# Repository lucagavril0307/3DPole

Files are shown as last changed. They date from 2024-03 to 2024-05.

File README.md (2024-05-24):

# 3DPole

10.04.2024 -> S-a adăugat un model CAD complet (dimensiunile pot diferi în viața reală, componentele pot diferi în viața reală, nu s-au făcut cablaje și/sau animații în modelul CAD)

11.04.2024 -> S-a adaugat un folder cu manuale ale componentelor, scheme electrice și/sau alte informații legale.

21.05.2024 -> S-a adăugat diagrama de cablare completă ( nu știu cum am ratat asta:3 );

23.05.2024 -> Configurația finală* a software-ului a fost publicată
- Este încă o versiune beta, testarea trebuie făcută pentru Marlin 2.1.x în sine și pentru configurația mea.

  24.05.2024 -> S-a adăugat noua documentaie în română precum și s-au făcut update-uri la documente deja existente.

3D Pole este o imprimanta 3 bazată pe Coordonate Polare construită din materiale “off-the-shelf” și/sau printate 3D.

## Proiectat de Luca Szilagyi de la Colegiul Național “Vasile Lucaciu” Baia Mare sub coordonarea dnei. profesoare Filip Adela

Toate fișierele pentru fișierele imprimabile 3D sunt furnizate în folderul 3D CAD, soft-ul este furnizat în folderul Software (configurația se afla sub irectorul Marlin, mai precis Configuration.h si Configuration_adv.h)

Acest proiect a necesitat piese imprimate 3D personalizate, precum și cabluri sertizate personalizate și firmware configurabil bazat pe Marlin.

!! Imprimanta dispune de protecție termică, dar este încă un prototip, așa că fiți conștienți de riscuri!

!! Sistemul folosește o sursă de alimentare de 24V 12,4 A. În timp ce metaluli firelor nu este expus, este totuși periculos!

# Imprimante Polare

Majoritatea oamenilor au auzit de imprimantele 3D Cartesiane, iar alții știu și despre imprimantele CoreXY.
Adevărul este că toată industria imprimării 3D s-a schimbat foarte mult în ultimii 20 de ani. Avem tipuri aparent nesfârșite de imprimante 3D.

Există imprimante carteziene normale care au crescut odată cu producția chineză de imprimante 3D după expirarea brevetului, există și imprimante CoreXY care au devenit mai populare la mijlocul anului 2020 și imprimantele Delta care au înregistrat o creștere în 2011 și încă una în 2024 odată cu lansarea. de imprimante rapide de la Flsun.

Fiecare tip de imprimantă are propriile defecte și puncte de vânzare, tipul cartezian de imprimantă este ieftină și ușor de întreținut, este, de asemenea, ușor de construit dacă doriți, dar nu este rapidă și multe probleme de calitate a vieții apar cu timpul. CoreXY sunt (cel mai adesea) mari, rapide și în general, dezavantajul lor este prețul și sistemul complex de mișcare. Imprimantele Delta sunt înalte și subțiri, la prima vedere înfricoșătoare, dar de fapt sunt mai rapide decât imprimantele carteziene (și modelele mai noi sunt chiar mai rapide decât cele CoreXY), ușor de întreținut, dar spațiul de imprimare este limitat și tind să fie destul de înalte și greu de incadrat intr-un spatiu normal.

Pe lângă aceste 3 tipuri majore de imprimante (când vorbim de mașini de tip FDM) există mașini cu 5 axe, CoreXZ, mașini de calitate industrială și preferatul meu , Imprimante Polaree.

Imprimantele Polare împrumută ceva de la toate cele 3 mari tipuri de imprimante FDM. Sunt ieftine și ușor de asamblat precum imprimantele carteziene, rapide* și fiabile ca frații lor CoreXY, ușor de extins și cu aspect înfricoșător (când vine vorba de matematică), la fel ca imprimantele Delta.

*Deși pot fi rapide, acest prototip nu este nimic din toate acestea, am ales lentă și robustă, deoarece oferă cele mai bune rezultate, cu multe reglaje, puteți transforma acest proiect într-o mașină rapidă.

Imprimantele carteziene tradiționale folosesc (după cum sugerează și numele) un sistem cartezian standard cu 3 axe, aveți valoarea X care vă spune cât de stânga sau dreapta este un punct ,valoarea Y care determină mișcarea înainte și înapoi și variabila Z care dictează înălţimea. CoreXY este oarecum același, dar X și Y sunt un sistem 2 în 1 realizat folosind o rutare ingenioasă a curelelor care mișcă capul de imprimare cu precizie cu axa Z deplasând întregul pat în sus și-n jos. Imprimantele Delta au un pat fix  nu par să aibă 3 axe diferite, au 3 axe paralele conectate la capul de imprimare cu 3 brațe, prin deplasarea celor 3 axe în diferite moduri puteți ajunge în orice punct din spațiul de imprimare, deși spațiul de imprimare nu este un cilindru, ci mai mult un con la vârf datorită acestui sistem de mișcare.

Imprimantele Polare arată ca imprimantele carteziene (numai ca aspect) cu 3 axe separate, dar un ochi atent va vedea că axa X este mai scurtă decât de obicei. Datorită unui sistem de mișcare Polară, axa X trebuie să aibă doar jumătate din dimensiunea patului, reducând astfel costurile materialelor, greutatea pe axa de imprimare și făcând o călătorie completă mai rapidă.

imagine

Pentru a obține poziția unui punct în planul XY veți avea nevoie de un unghi și de o distanță (r și Θ), distanța ia valori de la 0 (punctul din mijloc al cercului) și raza cercului (jumătate din dimensiunea patului, deci va fi axa X) în timp ce Θ este un unghi (deci de la 0 la 360 <sau 2π în radiani>, adică rotația patului, deci axa Y). Axa Z dictează doar cât de înalt este punctul menționat.

 # Specificații și informații despre imprimantă

 După cum am explicat mai devreme, este o imprimantă Polară, cu unele caracteristici realizate folosind imprimarea 3D.
 Cum ar putea funcționa asta?
 În primele timpuri ale imprimării 3D a existat o comunitate numită RepRap care dorea să facă imprimarea 3D mai accesibilă, deoarece la acea vreme, era destinată doar industriei sau bogaților. Au proiectat imprimante care ar putea fi ieftine și suficient de bune pentru ca oricine să le facă,. La acel moment nu puteai cumpăra o imprimantă prefabricată, trebuia să o construiești singur. În această perioadă s-au făcut o mulțime de noi descoperiri care au adus imprimarea 3D la ceea ce este astăzi.
 
Comunitatea RepRap a fost o mulțime de entuziaști care au făcut ca proiectele de imprimante i să fie ușor de recreat. Deoarece nu aveau acces la echipamente industriale, majoritatea pieselor dintr-o imprimantă 3d trebuiau imprimate 3d. Ei au decis ca generația 1 de imprimante să fie făcute cu piese  imprimate 3d de la mașini industriale și următoarea generație de imprimante ar putea avea toate piesele de care au nevoie de la mașina de prima generație, așa că, cu o singură mașină puteți face alta care poate face altul și așa mai departe. Tendința a prins din urmă și chiar a ajuns în zilele noastre.
Echipa de design Voron, cunoscută pentru imprimantele lor rapide, are propriul program „Print it forward” în care (pentru o sumă de bani) cineva care are deja o imprimantă Voron va imprima piesele de care aveți nevoie (și piesele estetice dacă doriți) și mai târziu, puteți imprima aceleași piese pe aparatul dvs. pentru altcineva.

Captură de ecran 2024-05-21 192004

Am decis să fac acest proiect în același spirit cu toate piesele printate 3D pentru această imprimantă putând fi realizate pe noua imprimantă.
Unele decizii trebuiau luate în ceea ce privește designul, nu mi-au plăcut niciodată imprimantele voluminoase (sau cele închise - chiar dacă au multe plusuri - deși am una). Axa X este inspirată de axa Ender 3 din două mari motive, pentru a fi clar că împrumută ceva de la imprimantele carteziene și pentru că, dacă nu este stricat, de ce sa il repar?

Designul este testat în timp și cred că arată bine în contrast cu întreaga imprimantă.
În ceea ce privește celelalte părți, sunt modele noi făcute de mine, pe lângă hotend-ul care este un model HERO ME și montura pentru axa X-E0 Care este un Model Ender 3.

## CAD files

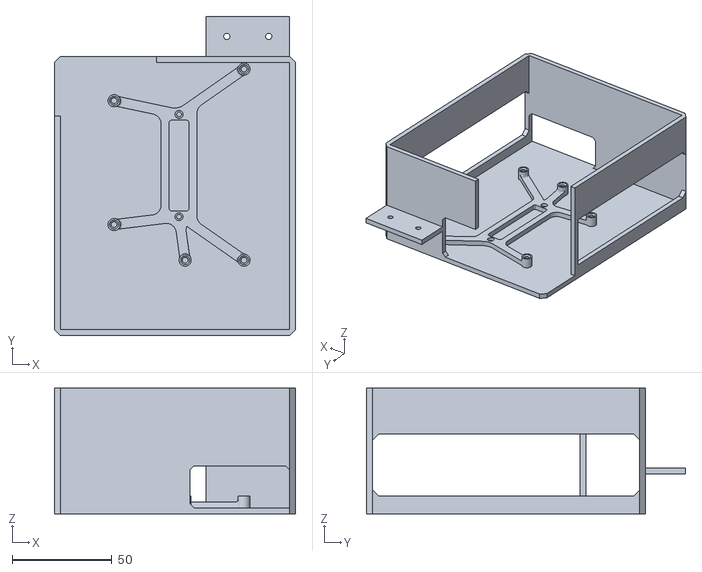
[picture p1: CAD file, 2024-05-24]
3DCADFiles/BTTCase.stl
121.0 x 160.0 x 63.0

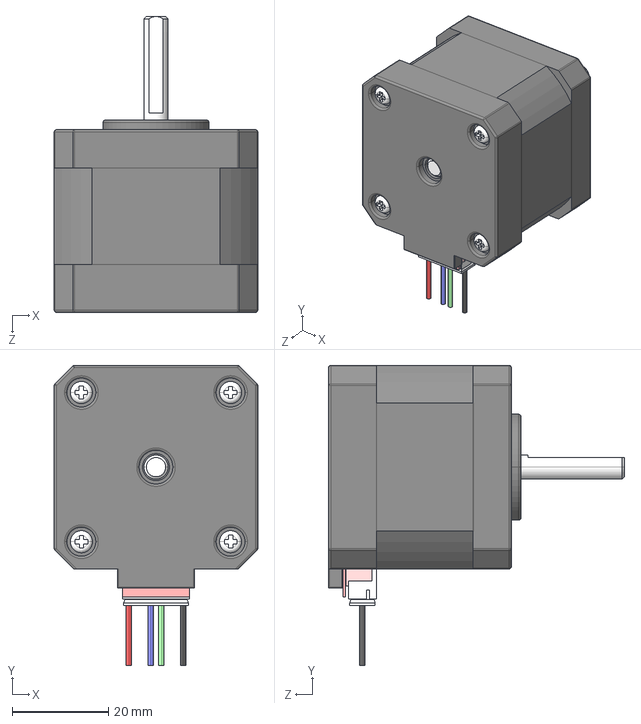
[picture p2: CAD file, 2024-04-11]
Wiring .Hardware Manuals and Documantation/17HE15-1504S.STEP
42.3 x 62.4 x 61.5 mm

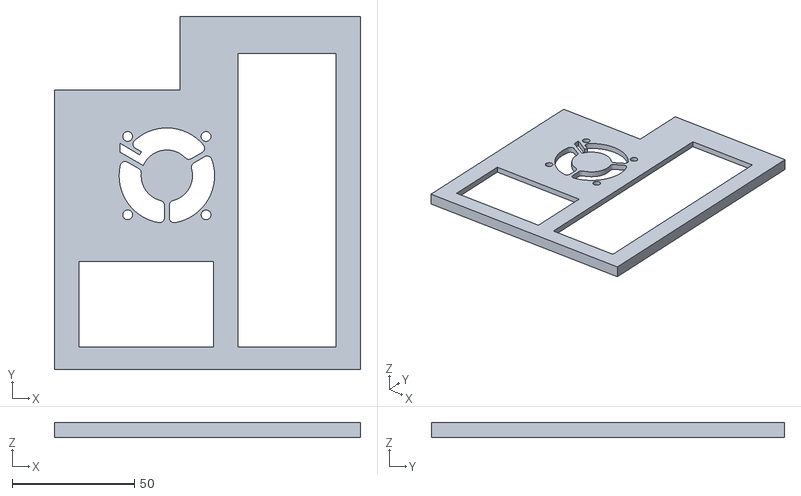
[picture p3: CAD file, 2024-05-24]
3DCADFiles/BTTTop.stl
125.2 x 144.2 x 6.00

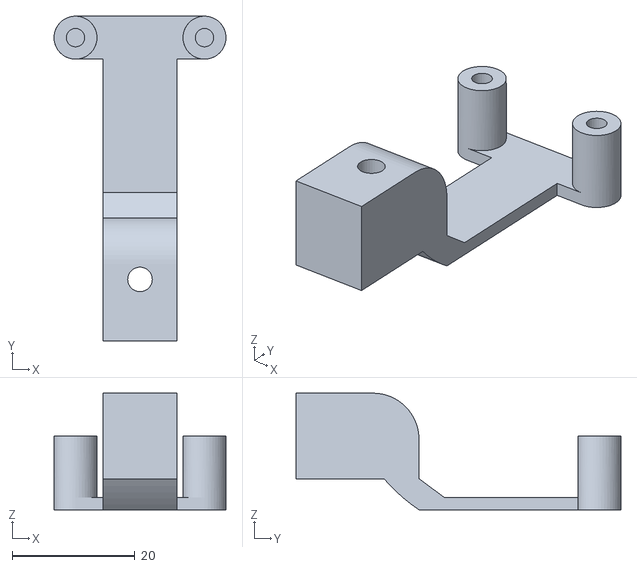
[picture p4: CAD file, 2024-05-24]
3DCADFiles/ZSwitch.stl
28.0 x 52.9 x 19.0

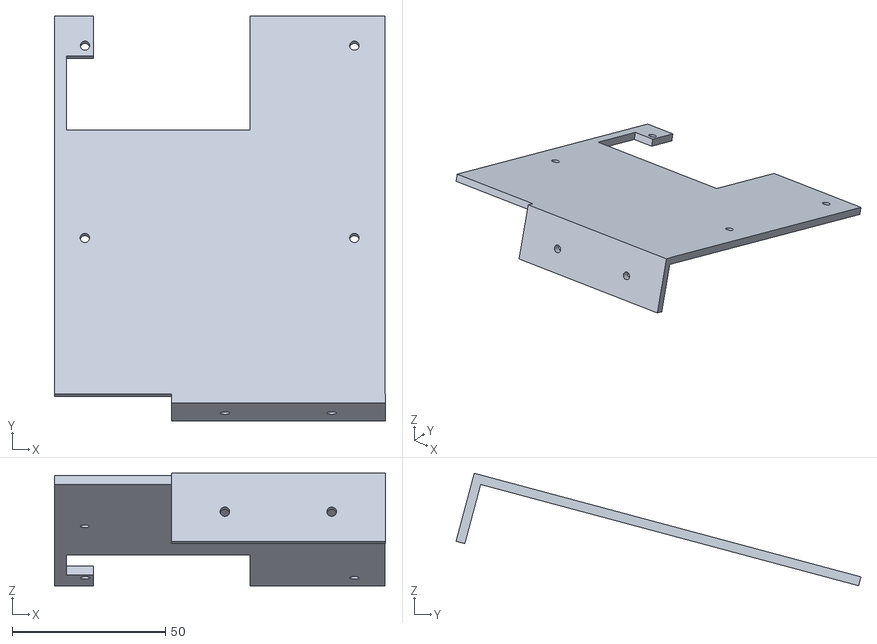
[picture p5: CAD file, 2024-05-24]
3DCADFiles/TFT35Case.stl
108.2 x 132.3 x 36.8

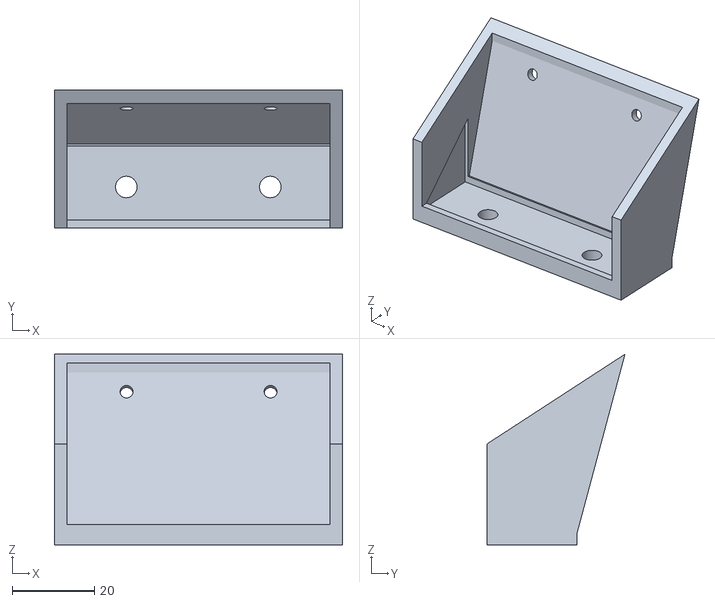
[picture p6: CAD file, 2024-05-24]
3DCADFiles/ScreenRiser.stl
70.2 x 33.6 x 46.5

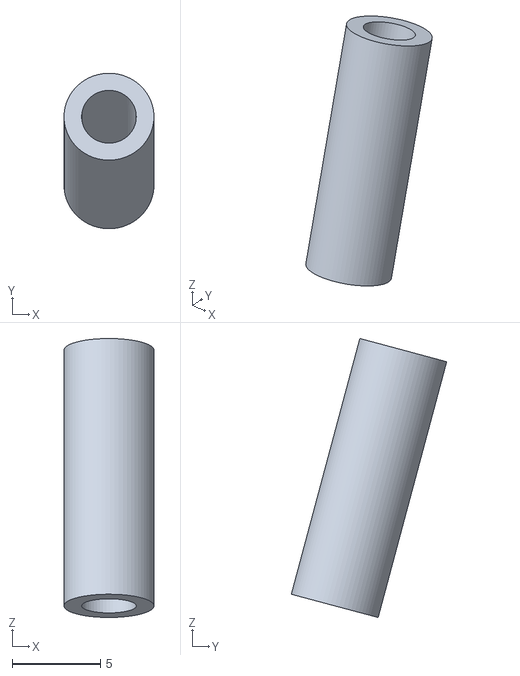
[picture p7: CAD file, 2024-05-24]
3DCADFiles/Standoff.stl
5.09 x 8.81 x 15.8

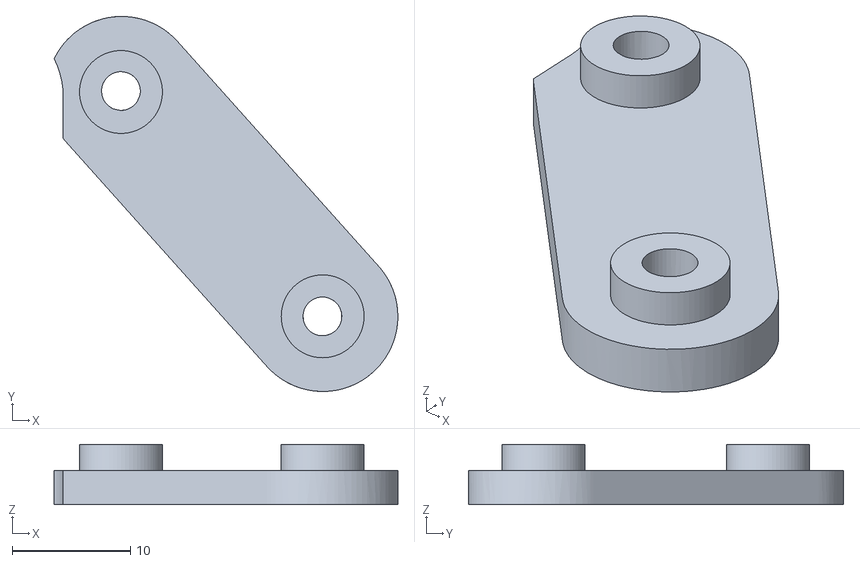
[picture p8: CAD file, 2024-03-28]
3DCADFiles/HOTENDBracket.stl
29.0 x 31.7 x 5.07

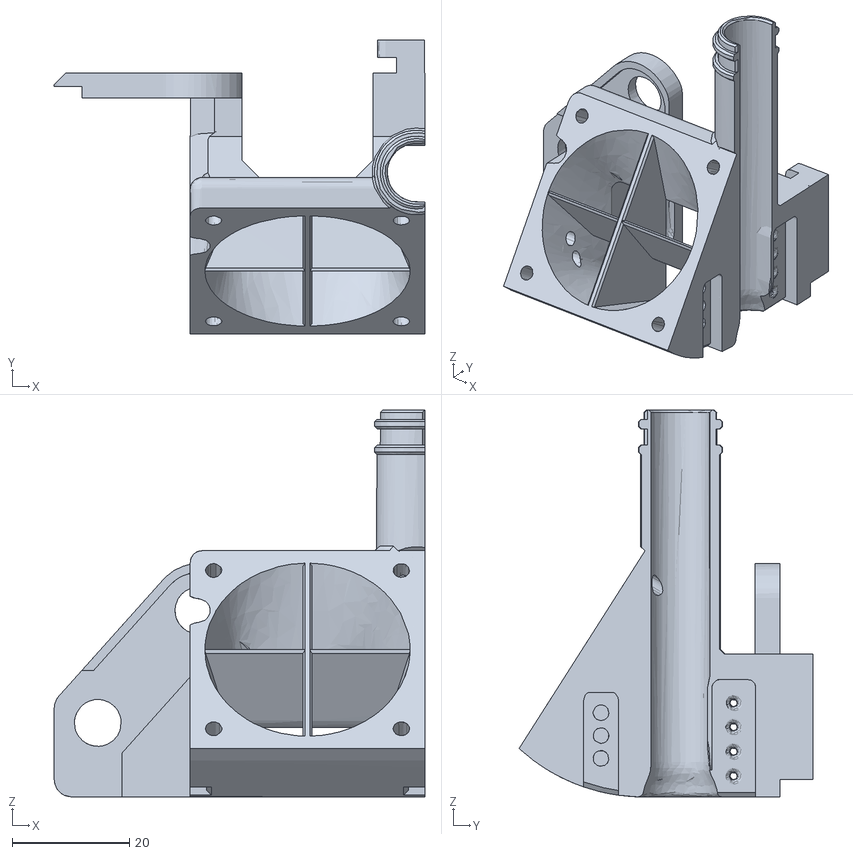
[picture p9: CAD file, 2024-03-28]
3DCADFiles/HOTENDMount1.stl
63.2 x 50.1 x 66.0

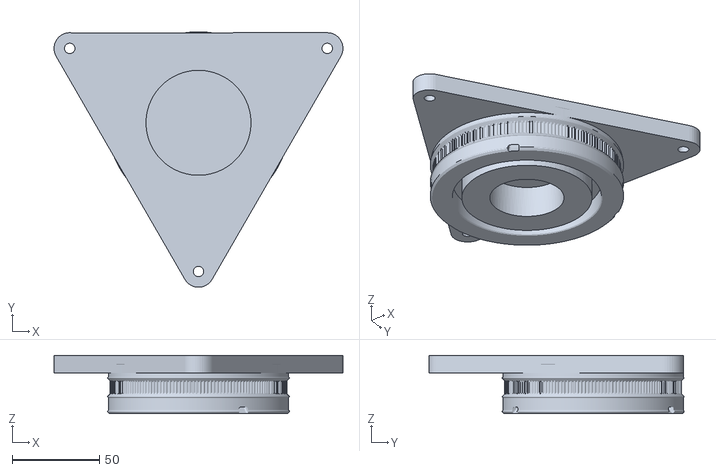
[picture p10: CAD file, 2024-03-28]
3DCADFiles/BEDBracket.stl
165.2 x 146.0 x 33.2

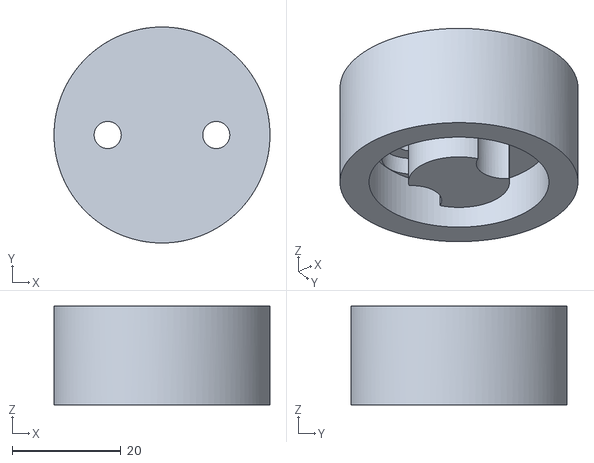
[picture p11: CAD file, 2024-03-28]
3DCADFiles/BEDMountAxis.stl
39.8 x 39.8 x 18.2

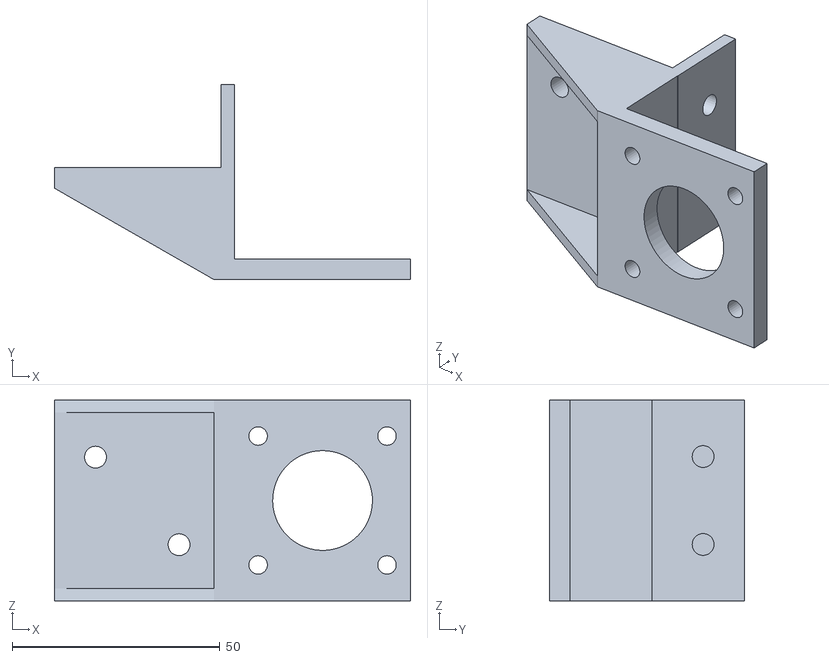
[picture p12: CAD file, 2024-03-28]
3DCADFiles/Y-MOTORMount v2.stl
85.6 x 47.0 x 48.3

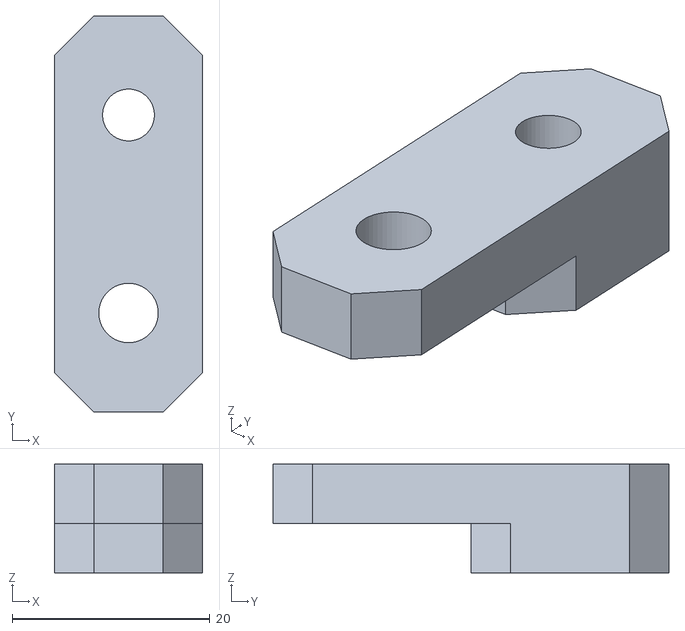
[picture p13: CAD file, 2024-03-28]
3DCADFiles/Belt Tensioner V1.stl
15.0 x 40.0 x 11.0

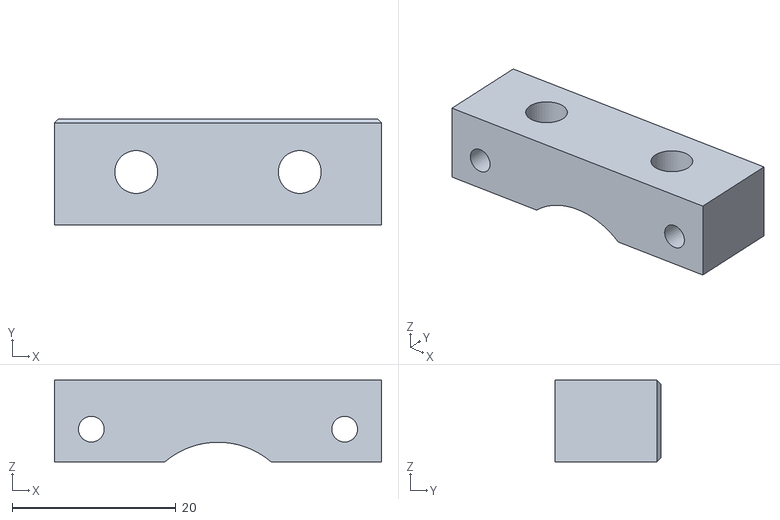
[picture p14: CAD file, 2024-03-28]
3DCADFiles/Z-MOTORMount.stl
40.0 x 13.0 x 10.0

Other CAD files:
3DCADFiles/PSUDoor.stl
3DCADFiles/HOTENDMount2.stl
3DCADFiles/PSUHousing.stl
3DCADFiles/BEDMOUNTExtender.stl
3DCADFiles/X-E0-MOTORBracket.stl

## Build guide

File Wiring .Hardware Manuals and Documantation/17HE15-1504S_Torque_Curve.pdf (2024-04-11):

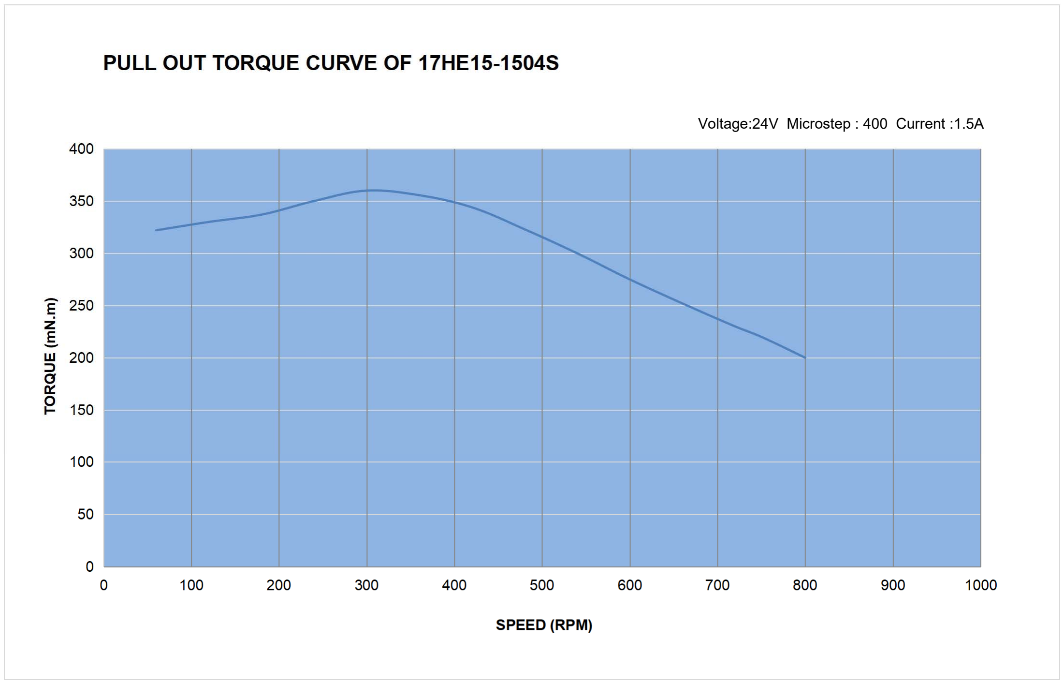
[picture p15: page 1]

Voltage:24V Microstep : 400 Current :1.5A

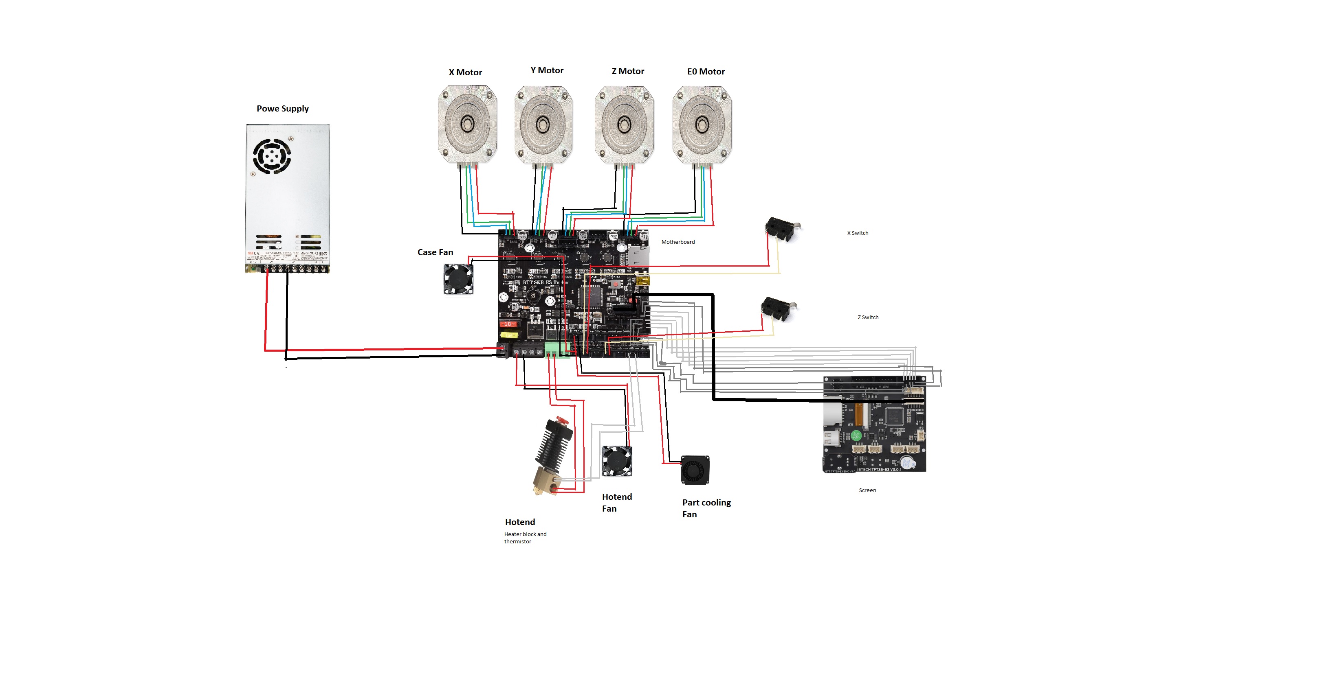
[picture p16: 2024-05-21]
Wiring .Hardware Manuals and Documantation/WiringDiagram.jpg

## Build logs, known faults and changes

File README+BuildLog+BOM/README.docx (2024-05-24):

Colegiul Național „Vasile Lucaciu”

3D Pole

Proiect dezvoltat de: Profesor coordonator

Szilagyi Luca Gavril Filip Adela

# Concept

3D Pole este o imprimanta 3D bazata pe coordonate Polar ce poate fi construita din piese ușor accesibile și piese printate 3D. Imprimanta a fost făcută în stil RepRap adică o imprimanta cu piese printate 3D ce se poate multiplica, adică prima imprimantă (numita și prima generație) conține piese printate pe alte mașinării ca mai apoi imprimanta de primă generație să printeze piesele pentru a 2-a generație ș.a.m.d.

În domeniul 3D există 3 mari tipuri de imprimante : imprimante carteziene, CoreXY sau Delta fiecare având derivate. Imprimantele Polare sunt speciale deoarece împrumută cate ceva de la fiecare dintre cele 3 mari tipuri : ca aparență este foarte asemănătoare cu o imprimantă Carteziană și una de tip Delta datorita axelor liniare X și Z și print patul rotund în formă de cerc, de la imprimantele CoreXY împrumută viteza[^1] și designul ingenios.

Coordonatele Polare se diferă de toate celelalte prin axa rotativă (in cazul nostru Y/U) care în loc de a folosi o valoare absolută liniară, folosește un unghi Θ, în timp ce axele X și Z rămân liniare. Axa X si Y lucrează in tandem spre a obține un sistem de mișcare asemănător cercului trigonometric :

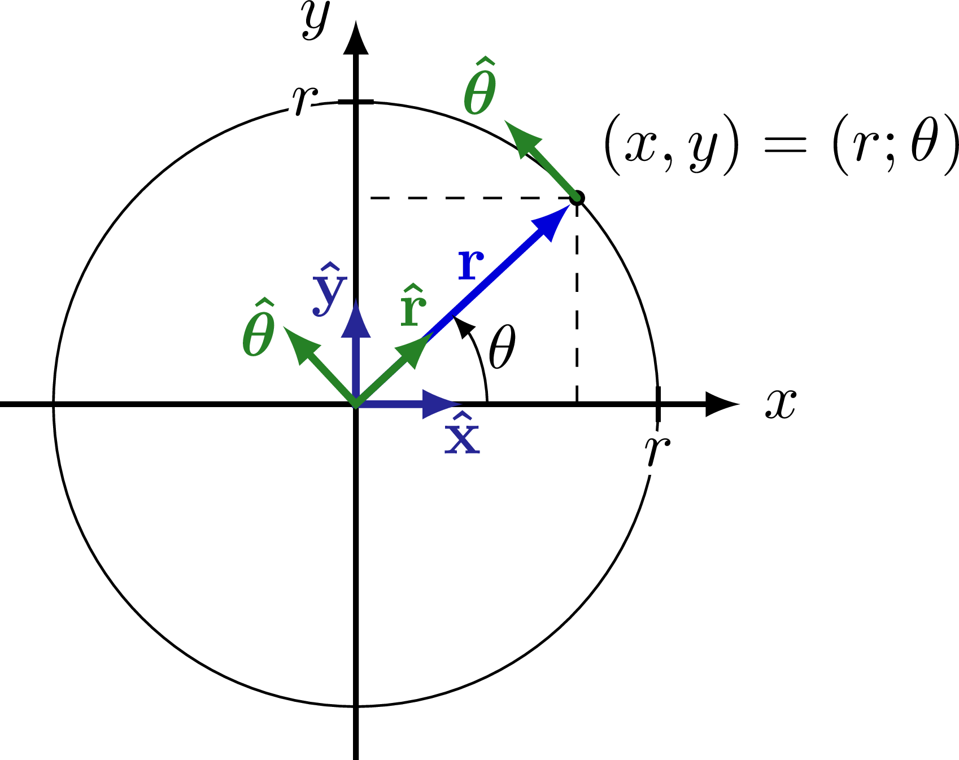
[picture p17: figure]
Polar coordinates & radians – TikZ.net

Vă puteți imagina axa X ca fiind linia trasată de r, adică distanța de la marginea cercului până la punctul la care trebuie să ajungem. Θ este dictat de axa Y astfel daca noi știm că trebuie să ajungem la punctul de unghi Θ=a și r=b, axa Y va roti cercul astfel încât unghiul să se afle sub axa X care se va mișca distanța r pentru a ajunge la punct. Axa Z dictează doar cât de sus se află punctul.

O mare diferență între acest tip de coordonate si cele carteziene sau CoreXY este lungimea axei X. În timp ce sistemele normale au nevoie de o axa X egală cu lungimea patului, sistemele polare au nevoie doar de jumătate de axă deoarece punctul diametral opus al axei X poate fi adus in raza de mișcare a axei respective prin rotirea axei Y.

# De ce 3D Pole?

Totul a început in anul 2023 când (fiind in căutarea unei imprimante 3D pentru uz personal) youtube mi-a recomandat un videoclip despre o imprimanta atât de compactă încât poate încăpea într-o cutie de filament numită Pozitron). Mi-a plăcut acel videoclip astfel că am început să caut online designeri ciudate de imprimante. Zilele următoare am dat de o pagină web „ascunsă” printre celelalte pagini ce se intitula „Circa Polar 3D Printer” creată de Willem Boshoff. Design-ul simplist mi-a plăcut de la început iar aceste coordonate polare păreau relativ relevante pentru mine (ținând cont ca in clasa a IX-a se preda cercul unitate in cadrul funcțiilor trigonometrice) astfel am început să mă documentez și am descoperit că acest tip de coordonate erau la momentul respectiv „moarte” datorita lipsei de interes și a apariției imprimantelor fabricate in masă la prețuri accesibile (ex: Ender 3). Am descoperit și alte proiecte asemănătoare : R-360, Sculpto^2 (care a fost si comercializată pentru scurt timp) și imprimanta polară a lui Rob Mink, toate proiecte abandonate în ziua de azi.

Am decis să încerc să arăt acest tip de imprimante si altor oameni, vouă, care poate nu o vor lăsa să dispară din nou.

La fel ca oricare proiect ambițios exista o grămadă de sânge și sudoare (la propriu sânge – am suferit multe leziuni in timp ce lucram pe proiect si destule șocuri electrice cât să îmi ajungă o viață) dar totul a meritat atunci când am văzut proiectul cum ia viață.

Pe parcursul developării proiectului am învățat destul de multe despre electricitate, componente electrice, codare și configurare Marlin și despre mult alte cunoștințe ce o să îmi prindă bine în viitor: cum să îmi sertizez propriile cabluri, ce face un design a fii ingenios, de ce nu folosim ca testbench o masă cu blat metalic (greșeala asta m-a costat o întreagă placă de control) și multe altele.

Am dorit totuși ca proiectul meu să fie special, a nu se asemăna cu vreun alt proiect menționat mai sus, desigur, ca și sistem de mișcare, coordonatele polare nu pot fi schimbate atât de drastic (deși am văzut un sistem polar întors) astfel că am decis folosirea pofilelor de aluminiu, a unei axe X inspirată de cea a unui Ender 3 (pentru a evidenția asemănarea intre cele 2 sisteme de mișcare) și totuși ca ea să aibă un twist doar al meu, am dorit implementarea unu pat încălzit (deși am eșuat in acest aspect – am un prototip de implementare a unu pat încălzit, dar acesta mai are nevoie de multe implementări pentru a fi sigur de utilizat problema principală fiind riscul de electrocutare – acest sistem este bazat pe ideea unui rulment axial prin care ar trece curentul, ținând cont ca bilele de metal au mereu contact cu firele legate de exteriorul rulmentului, unul dintre fire (cel legat de pat) se poate învârti la infinit fără a pierde continuitatea însă exista riscul ca plasticul de sub rulment să se topească datorita încălzirii rulmentului din cauza curentului electric ceea ce ar duce la un contact dintre rulment si scheletul imprimantei care daca nu ar arde orice alta componenta legată de schelet, ar reprezenta un pericol electric pentru utilizator).

Colorarea verde a fost o alegere complet aleatorie la început, acea culoare a fost filamentul pe care l-am folosit pentru primele prototipuri, iar in contrast cu negru mi-a plăcut atât de mult încât am decis ca aceasta culoare sa fie „tema” proiectului.

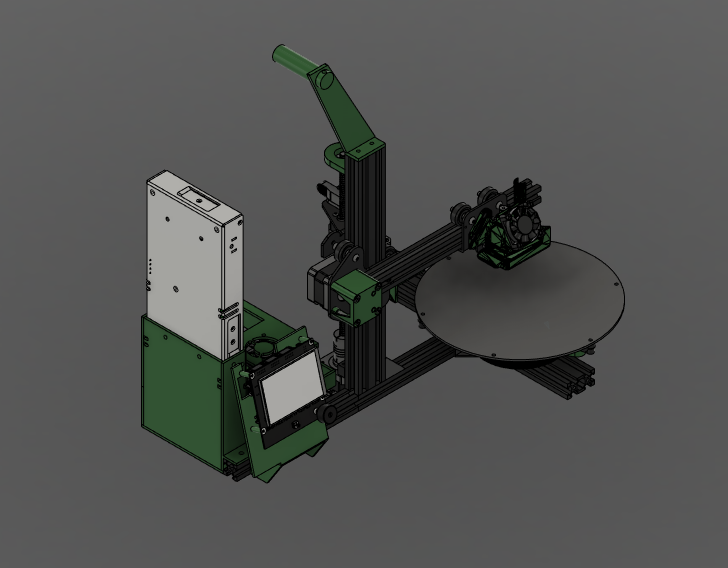
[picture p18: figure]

# Software și Hardware

Din punct de vedere software, imprimanta rulează Marlin 2.1.x bugfix configurat de mine pentru a completa cerințele necesare mie. Marlin Developing Team deține drepturile de autor pentru Marlin in sine, eu dețin doar titlu de autor al configurației făcute de mine.

În cazul în care se dorește modificarea codului din partea unei alte persoane (în scop personal) acest tip de modificări sunt permise, sau aducerea de modificări substanțiale codului, persoana respectivă va deține dreptul asupra configurațiilor sale specifice.

Cele 2 fișiere Configuration.h și Configuration_adv.h se găsesc in folderul Software/Marlin-bugfix-2.1.x sub directorul Marlin. În cazul în care nu știți ceea ce faceți se recomandă modificarea doar a fișierului Configuration.h deoarece in cealaltă configurare, unele setări pot să îți strice permanent componentele sau placa de bază în sine în cazul în care este configurată necorespunzător .

Pentru adaptarea fișierului Configuration.h puteți folosi VSCode împreună cu platform.io sau Marlin Builder (personal folosesc platform.io) iar pentru plăcuțele cu cipuri de 8 biți se poate folosi și Arduino IDE. Vor trebui modificate, după caz, :

- placa de bază ce poate fi găsită la :

#ifndef MOTHERBOARD

#define MOTHERBOARD BOARD_BTT_SKR_E3_TURBO

#endif

- porturile seriale : (0 pentru SD card, -1 pentru USB ) :

#define SERIAL_PORT 0

#define SERIAL_PORT_2 -1

- distanța de deplasare a axelor :

#define X_BED_SIZE 110

#define Y_BED_SIZE 110

- tipul de ecran folosit : (se găsește în secțiunea Screen – nu pot arăta o singură comandă deoarece există sute de tipuri de ecrane din care poți alege)
- Sistemul de mișcare folosit ( configurația poate fi modificată pentru orice sistem de mișcare doar că alte setări mai ascunse vor trebui să fie modificate, pe moment, explic o formatare generală) ce se găsește la secțiunea Mechanical Settings.

Majoritatea codului are comentarii puse de developer în limba engleză dar pentru a face un scurt rezumat, se declară coordonatele Polare mărimea fizică a imprimantei, sensul motoarelor, endswitch-urile, senzorii de temperatură, ecranul folosit, pinii pentru ventilatoare, se configurează Thermal Runaway Protection (funcție ce ar trebui să prevină eventuale riscuri de incendiu datorate de funcționarea incorectă a senzorilor de temperatură !! atenție, TRP nu asigură ca accidente nu se pot întâmpla, totul are riscuri) și multe alte setări care la rândul lor sunt mai mult decât importante pentru buna funcționare a Software-ului.

Din punct de vedere hardware, proiectul este compus din profile de aluminiu, componente mecanice, piese printate 3D și componente electronice.

Un Bill Of Materials (adică un tabel cu piesele necesare – excluzând numărul de șurube și alte lucruri considerate miscellaneous – adică de care ai nevoie dar sunt puține, obscure sau unelte de care vei avea nevoie nu sunt specificate în BOM). Totodată unele componente vor suferi schimbări (spre exemplu profilul 20x20 V slot de 30 de cm de pe axa X care va fi tăiat la mărimea de ~ 21 de cm) sau piulița trapezoidală care va trebui îngustată cu 2 mm. Aceste modificări pot fi evitate daca se achiziționează profile pre tăiate sau o piuliță cu montare in 2 puncte (nu în 4 ca și in cazul meu)

Trebuie menționat că majoritatea pieselor printate 3D sunt design-ul meu personal cu excepția : X-E0-MOTORMount care este un montaj Ender 3 doar că printat 3D și întregul Hotend care este un HERO ME Ender 3 Fan Duct re-model cu modificări minime, hotend al cărui designer este MediaMan3D si re-designer Beegeemon.

DISCLAIMER: Robotul real poate diferii de Modelul CAD complet și viceversa, se fac update-uri permanent la ambele versiuni (fizică și digitală) doar că fișierele nu sunt întotdeauna puse pe GitHub.

Software-ul a fost uploadat doar în data de 23.05.2024 deoarece versiunile precedente erau mai mult decât experimentale și nu puteau fi folosite decât in scop pur personal.

## Resurse :

- Logo făcut cu ajutorul : https://www.wix.com/logo/maker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 (https://www.wix.com/logo/maker?gad_source=1)
- Circa Polar Printer :

https://www.wix.com/logo/maker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 (https://www.wix.com/logo/maker?gad_source=1)

- R-360:

https://reprap.org/wiki/R_360

- Sculpto^2:

https://sculpto-shop.com/products/sculpto-pro2-3d-printer

- Poză coordonate polare:

https://tikz.net/circle/

- Marlin Github:

https://github.com/MarlinFirmware/Marlin

- Hero Me Mount (re-design):

https://www.thingiverse.com/thing:3991855

[^1] - -» viteza este un concept relativ, deși în teorie o imprimantă polară ar trebui să fie mai rapida ca cele carteziene, totul depinde de configurația softului. Personal am ales să rulez viteze moderate pentru rezultate decente dar cu multă muncă, se pot atinge viteze ridicate.

2 Szilagyi Luca Colegiul Național „Vasile Lucaciu”

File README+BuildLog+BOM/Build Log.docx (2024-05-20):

Build Log

3 februarie 2024

- primul concept de rama al imprimantei – asemanator cu un L și un picior din V-Slot 2040 cu un stalp vertical tot din V-Slot 2040 , un brat din V-Slot 2020 (neconectat la rama momentan) și un conector picior-stalp din V-slot 2020 toate marimile sunt de 30 cm conectate prin unghiuri de sustinere și suruburi cu piulite T-Slot M5.
- a se taia la finalizarea modelului complet
- începerea modelului 3D în Fusion 360

6 februarie 2024

- Montajul -parțial- al axei X : Montura de metal fata, montura printata 3d spate (PLA) 3 suruburi M5 cu 6 tuburi de spatiere și 3 roti V-slot, T-nut și motorul principal axa X + brațul axei X montat prin 2 suruburi M4.
  a se cumpara o piulita excentrica pentru aranjare roților pe profil
- Transpunerea lucrărilor în Fusion.

7 februarie 2024

- Asamblarea extruderului ( un motor nema 17, trei șuruburi de prindere, 2 componente ale extruderului, arcul de tensiune, rulmentul cu cale de filament, roata zimtata) si roata GT pe motorul X.
- Transpunerea lucrărilor în Fusion.

10 februarie 2024

- Asamblarea axei Z (un motor nema 17, un cuplaj, o piesa de montare a motorului la V-Slot cu 2 suruburi M5 și două M4)\
  a se monta un stabilizator a surubului trapezoidal
- Atasarea axei Z la rama imprimantei, montarea axei X-E0 la rama imprimantei.
- Începerea prototipizarii asupra unei monturi de pat.

v1.0 - spațiile de montare nu se potrivesc

v1.1 - montura are locuri slabe ce ar ceda ușor

v2.0 - deși montura e rezistenta, în cazul în care doresc sa adaug un pat încălzit, va fi greu de implementat

v2.1 - aceeasi montura ca si in v2.0 dar cu adaptoare de montare ce ridica patul și permit dezinstalarea ușoară a acestuia

Deși asupra monturii v2.1 se vor aplica și alte schimbări, ele nu sunt relevante (unele schimbări estetice, alte de tip QOL (quality of life) )

- Transpunerea lucrărilor în Fusion.

17-20 februarie 2024

- Montarea patului rotativ, a motorului pentru axa Y, stabilizator a surubului trapezoidal, capului de printare și a curelei + tensionator pentru axa X.
- Incepeara prototipizarii pentru monturile electronice.
  a se achizitiona o curea inchisa de 610mm pentru axa Y
- original proiectul folosea un Arduino Mega și un Ramps 1.4 shield modificat la 24V, componenta din urma a luat foc în urma unui scurtcircuit provocat de o eroare de fabricație, analizând internetul am descoperit ca placa nu este foarte sigură (în special modificată la 24V) și totodată, Arduino Mega, deși o placă de dezvoltare buna, nu ar putea face fata calculelor necesare unui sistem Polar astfel s-a decis achiziționarea unei placute BTT SKR E3 Turbo second-hand (desigur, nu înainte de a arde alte 2 placute Ramps și de a solicita placuta Arduino Mega pana cand aceasta a refuzat sa se mai porneasca)
- Transpunerea lucrărilor în Fusion.

20 februarie 2024 - 8 Martie 2024

- Perioada de inactivitate

9 - 22 Martie 2024

- Finalizarea prototipizarii pentru monturile de componente electrice, începerea de legare a firelor (și de compunere a propriile fire), începerea de lucrare pe software.
- Software - Marlin (versiuni vechi și noi) modificate pentru imprimanta mea Polara, Pronterface pentru trimitere de comenzi (accesibil momentan doar în cazul în care imprimanta nu este asamblată).
- Finalizarea lucrărilor în Fusion, deschiderea unui repository in GitHub (si ulterior uploadarea modelelor de piese ce pot fi printate 3D)

Aprilie 2024

- Continuarea cu o nouă versiune de software v2.0 schimbată fata de v1.0.
- Finisarea lucrărilor în CAD
- Uploadarea Manualelor de utilizare, a datelor tehnice și a unui model CAD complet în CAD împreuna cu un Bill of Material (BOM) în GitHub.

Martie 2024

- Finalizarea documentației proiectului, updatarea fișierului README pentru a oferi o reprezentare mai buna a proiectului, lucrări de finisare asupra imprimantei (asortarea componentelor, rezolvarea monturilor improvizate)
- A se uploada documentația și configurația Marlin pana-n saptamana intre 19 -26 Martie —-> Configurația Marlin nu a fost publicată în variațiile precedente (momentan configurația se afla la v3.1) deoarece versiunile precedente au fost de tip Alpha și doar pentru testare.

Propuneri viitoare

- adaptarea unui modul Wifi pentru comunicare wireless
- Trecerea de la Marilin la RepRapFirmware (RRF)
- Configurarea unui Pat Încălzit (cu ajutorul unui modul asemănător unui rulment dar și unui cerc de alunecare)
- Configurarea imprimantei pentru viteze ridicate

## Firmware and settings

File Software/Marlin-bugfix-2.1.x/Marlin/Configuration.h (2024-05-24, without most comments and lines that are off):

#pragma once
#define CONFIGURATION_H_VERSION 02010300
#define STRING_CONFIG_H_AUTHOR "Szilagyi Luca" // Who made the changes.
  #define MOTHERBOARD BOARD_BTT_SKR_E3_TURBO
#define SERIAL_PORT 0
#define BAUDRATE 115200
#define SERIAL_PORT_2 -1
#define CUSTOM_MACHINE_NAME "3DPole"
#define X_DRIVER_TYPE  TMC2209
#define Y_DRIVER_TYPE  TMC2209
#define Z_DRIVER_TYPE  TMC2209
#define E0_DRIVER_TYPE TMC2209
#define EXTRUDERS 1
#define DEFAULT_NOMINAL_FILAMENT_DIA 1.75
#define TEMP_SENSOR_0 1
#define TEMP_SENSOR_1 0
#define TEMP_SENSOR_2 0
#define TEMP_SENSOR_3 0
#define TEMP_SENSOR_4 0
#define TEMP_SENSOR_5 0
#define TEMP_SENSOR_6 0
#define TEMP_SENSOR_7 0
#define TEMP_SENSOR_BED 0
#define TEMP_SENSOR_PROBE 0
#define TEMP_SENSOR_CHAMBER 0
#define TEMP_SENSOR_COOLER 0
#define TEMP_SENSOR_BOARD 0
#define TEMP_SENSOR_SOC 0
#define TEMP_SENSOR_REDUNDANT 0
#define DUMMY_THERMISTOR_998_VALUE  25
#define DUMMY_THERMISTOR_999_VALUE 100
#if TEMP_SENSOR_IS_MAX_TC(0)
  #define MAX31865_SENSOR_OHMS_0      100 // (Ω) Typically 100 or 1000 (PT100 or PT1000)
  #define MAX31865_CALIBRATION_OHMS_0 430 // (Ω) Typically 430 for Adafruit PT100; 4300 for Adafruit PT1000
#endif
#if TEMP_SENSOR_IS_MAX_TC(1)
  #define MAX31865_SENSOR_OHMS_1      100
  #define MAX31865_CALIBRATION_OHMS_1 430
#endif
#if TEMP_SENSOR_IS_MAX_TC(2)
  #define MAX31865_SENSOR_OHMS_2      100
  #define MAX31865_CALIBRATION_OHMS_2 430
#endif
#if HAS_E_TEMP_SENSOR
  #define TEMP_RESIDENCY_TIME         10  // (seconds) Time to wait for hotend to "settle" in M109
  #define TEMP_WINDOW                  1  // (°C) Temperature proximity for the "temperature reached" timer
  #define TEMP_HYSTERESIS              3  // (°C) Temperature proximity considered "close enough" to the target
#endif
#if TEMP_SENSOR_BED
  #define TEMP_BED_RESIDENCY_TIME     10  // (seconds) Time to wait for bed to "settle" in M190
  #define TEMP_BED_WINDOW              1  // (°C) Temperature proximity for the "temperature reached" timer
  #define TEMP_BED_HYSTERESIS          3  // (°C) Temperature proximity considered "close enough" to the target
#endif
#if TEMP_SENSOR_CHAMBER
  #define TEMP_CHAMBER_RESIDENCY_TIME 10  // (seconds) Time to wait for chamber to "settle" in M191
  #define TEMP_CHAMBER_WINDOW          1  // (°C) Temperature proximity for the "temperature reached" timer
  #define TEMP_CHAMBER_HYSTERESIS      3  // (°C) Temperature proximity considered "close enough" to the target
#endif
#if TEMP_SENSOR_REDUNDANT
  #define TEMP_SENSOR_REDUNDANT_SOURCE    E1  // The sensor that will provide the redundant reading.
  #define TEMP_SENSOR_REDUNDANT_TARGET    E0  // The sensor that we are providing a redundant reading for.
  #define TEMP_SENSOR_REDUNDANT_MAX_DIFF  10  // (°C) Temperature difference that will trigger a print abort.
#endif
#define HEATER_0_MINTEMP   5
#define HEATER_1_MINTEMP   5
#define HEATER_2_MINTEMP   5
#define HEATER_3_MINTEMP   5
#define HEATER_4_MINTEMP   5
#define HEATER_5_MINTEMP   5
#define HEATER_6_MINTEMP   5
#define HEATER_7_MINTEMP   5
#define BED_MINTEMP        5
#define CHAMBER_MINTEMP    5
#define HEATER_0_MAXTEMP 275
#define HEATER_1_MAXTEMP 275
#define HEATER_2_MAXTEMP 275
#define HEATER_3_MAXTEMP 275
#define HEATER_4_MAXTEMP 275
#define HEATER_5_MAXTEMP 275
#define HEATER_6_MAXTEMP 275
#define HEATER_7_MAXTEMP 275
#define BED_MAXTEMP      150
#define CHAMBER_MAXTEMP  60
#define HOTEND_OVERSHOOT 15   // (°C) Forbid temperatures over MAXTEMP - OVERSHOOT
#define BED_OVERSHOOT    10   // (°C) Forbid temperatures over MAXTEMP - OVERSHOOT
#define COOLER_OVERSHOOT  2   // (°C) Forbid temperatures closer than OVERSHOOT
#define PIDTEMP           // See the PID Tuning Guide at https://reprap.org/wiki/PID_Tuning
#define PID_MAX  255      // Limit hotend current while PID is active (see PID_FUNCTIONAL_RANGE below); 255=full current
#define PID_K1     0.95   // Smoothing factor within any PID loop
    #define DEFAULT_Kp  22.20
    #define DEFAULT_Ki   1.08
    #define DEFAULT_Kd 114.00
#define MAX_BED_POWER 255 // limits duty cycle to bed; 255=full current
#define MAX_CHAMBER_POWER 255 // limits duty cycle to chamber heater; 255=full current
  #define PID_FUNCTIONAL_RANGE 10 // If the temperature difference between the target temperature and the actual temperature
#define PREVENT_COLD_EXTRUSION
#define EXTRUDE_MINTEMP 170
#define PREVENT_LENGTHY_EXTRUDE
#define EXTRUDE_MAXLENGTH 200
#define THERMAL_PROTECTION_HOTENDS // Enable thermal protection for all extruders
#define THERMAL_PROTECTION_BED     // Enable thermal protection for the heated bed
#define THERMAL_PROTECTION_CHAMBER // Enable thermal protection for the heated chamber
#define THERMAL_PROTECTION_COOLER  // Enable thermal protection for the laser cooling
#define POLAR
  #define DEFAULT_SEGMENTS_PER_SECOND 180   // If movement is choppy try lowering this value
  #define PRINTABLE_RADIUS 82.0f            // (mm) Maximum travel of X axis
  #define POLAR_FAST_RADIUS 3.0f            // (mm)
  #define POLAR_CENTER_OFFSET 0.0f          // (mm)
  #define FEEDRATE_SCALING                  // Convert XY feedrate from mm/s to degrees/s on the fly
#define ENDSTOPPULLUPS
#define X_MIN_ENDSTOP_HIT_STATE LOW
#define X_MAX_ENDSTOP_HIT_STATE HIGH
#define Y_MIN_ENDSTOP_HIT_STATE HIGH
#define Y_MAX_ENDSTOP_HIT_STATE HIGH
#define Z_MIN_ENDSTOP_HIT_STATE LOW
#define Z_MAX_ENDSTOP_HIT_STATE HIGH
#define I_MIN_ENDSTOP_HIT_STATE HIGH
#define I_MAX_ENDSTOP_HIT_STATE HIGH
#define J_MIN_ENDSTOP_HIT_STATE HIGH
#define J_MAX_ENDSTOP_HIT_STATE HIGH
#define K_MIN_ENDSTOP_HIT_STATE HIGH
#define K_MAX_ENDSTOP_HIT_STATE HIGH
#define U_MIN_ENDSTOP_HIT_STATE HIGH
#define U_MAX_ENDSTOP_HIT_STATE HIGH
#define V_MIN_ENDSTOP_HIT_STATE HIGH
#define V_MAX_ENDSTOP_HIT_STATE HIGH
#define W_MIN_ENDSTOP_HIT_STATE HIGH
#define W_MAX_ENDSTOP_HIT_STATE HIGH
#define Z_MIN_PROBE_ENDSTOP_HIT_STATE HIGH
#define DEFAULT_AXIS_STEPS_PER_UNIT   { 100, 66.66666666666667, 200, 415 }
#define EDITABLE_STEPS_PER_UNIT
#define DEFAULT_MAX_FEEDRATE          { 400, 350, 100, 50 }
#define DEFAULT_MAX_ACCELERATION      { 2000, 1500, 500, 10000 }
#define DEFAULT_ACCELERATION          2000    // X, Y, Z and E acceleration for printing moves
#define DEFAULT_RETRACT_ACCELERATION  2000    // E acceleration for retracts
#define DEFAULT_TRAVEL_ACCELERATION   2000    // X, Y, Z acceleration for travel (non printing) moves
#define CLASSIC_JERK
  #define DEFAULT_XJERK 10.0
  #define DEFAULT_YJERK 10.0
  #define DEFAULT_ZJERK  2.0
  #define DEFAULT_EJERK  10.0
#define Z_MIN_PROBE_USES_Z_MIN_ENDSTOP_PIN
#define NOZZLE_TO_PROBE_OFFSET { 10, 10, 0 }
#define PROBING_TOOL 0
#define PROBING_MARGIN 10
#define XY_PROBE_FEEDRATE (133*60)
#define Z_PROBE_FEEDRATE_FAST (4*60)
#define Z_PROBE_FEEDRATE_SLOW (Z_PROBE_FEEDRATE_FAST / 2)
#define Z_CLEARANCE_DEPLOY_PROBE   10 // (mm) Z Clearance for Deploy/Stow
#define Z_CLEARANCE_BETWEEN_PROBES  5 // (mm) Z Clearance between probe points
#define Z_CLEARANCE_MULTI_PROBE     5 // (mm) Z Clearance between multiple probes
#define Z_PROBE_ERROR_TOLERANCE     3 // (mm) Tolerance for early trigger (<= -probe.offset.z + ZPET)
#define Z_PROBE_LOW_POINT          -2 // (mm) Farthest distance below the trigger-point to go before stopping
#define X_ENABLE_ON 0
#define Y_ENABLE_ON 0
#define Z_ENABLE_ON 0
#define E_ENABLE_ON 0 // For all extruders
#define DISABLE_X
#define DISABLE_Y
#define DISABLE_Z
#define DISABLE_E               // Disable the extruder when not stepping
#define DISABLE_OTHER_EXTRUDERS   // Keep only the active extruder enabled
#define INVERT_X_DIR true
#define INVERT_Y_DIR true
#define INVERT_Z_DIR false
#define INVERT_E0_DIR true
#define INVERT_E1_DIR false
#define INVERT_E2_DIR false
#define INVERT_E3_DIR false
#define INVERT_E4_DIR false
#define INVERT_E5_DIR false
#define INVERT_E6_DIR false
#define INVERT_E7_DIR false
#define X_HOME_DIR -1
#define Y_HOME_DIR -1
#define Z_HOME_DIR -1
#define X_BED_SIZE 110
#define Y_BED_SIZE 110
#define X_MIN_POS 0
#define Y_MIN_POS 0
#define Z_MIN_POS 0
#define X_MAX_POS X_BED_SIZE
#define Y_MAX_POS Y_BED_SIZE
#define Z_MAX_POS 175
#define MIN_SOFTWARE_ENDSTOPS
  #define MIN_SOFTWARE_ENDSTOP_X
  #define MIN_SOFTWARE_ENDSTOP_Z
  #define MIN_SOFTWARE_ENDSTOP_I
  #define MIN_SOFTWARE_ENDSTOP_J
  #define MIN_SOFTWARE_ENDSTOP_K
  #define MIN_SOFTWARE_ENDSTOP_U
  #define MIN_SOFTWARE_ENDSTOP_V
  #define MIN_SOFTWARE_ENDSTOP_W
#define MAX_SOFTWARE_ENDSTOPS
  #define MAX_SOFTWARE_ENDSTOP_X
  #define MAX_SOFTWARE_ENDSTOP_Z
  #define MAX_SOFTWARE_ENDSTOP_I
  #define MAX_SOFTWARE_ENDSTOP_J
  #define MAX_SOFTWARE_ENDSTOP_K
  #define MAX_SOFTWARE_ENDSTOP_U
  #define MAX_SOFTWARE_ENDSTOP_V
  #define MAX_SOFTWARE_ENDSTOP_W
#define BED_CENTER_AT_0_0
#define HOMING_FEEDRATE_MM_M { (50*60), (50*60), (10*60) }
#define VALIDATE_HOMING_ENDSTOPS
#define EEPROM_SETTINGS     // Persistent storage with M500 and M501
#define EEPROM_CHITCHAT       // Give feedback on EEPROM commands. Disable to save flash.
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

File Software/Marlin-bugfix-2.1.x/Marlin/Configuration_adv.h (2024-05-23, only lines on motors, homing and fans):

#define E0_AUTO_FAN_PIN -1
#define E1_AUTO_FAN_PIN -1
#define E2_AUTO_FAN_PIN -1
#define E3_AUTO_FAN_PIN -1
#define E4_AUTO_FAN_PIN -1
#define E5_AUTO_FAN_PIN -1
#define E6_AUTO_FAN_PIN -1
#define E7_AUTO_FAN_PIN -1
#define CHAMBER_AUTO_FAN_PIN -1
#define COOLER_AUTO_FAN_PIN -1
#define HOMING_BUMP_MM      { 5, 5, 5 }       // (linear=mm, rotational=°) Backoff from endstops after first bump
#define HOMING_BUMP_DIVISOR { 2, 2, 2 }       // Re-Bump Speed Divisor (Divides the Homing Feedrate)
#define MICROSTEP_MODES { 16, 16, 16, 16, 16, 16 } // [1,2,4,8,16]
#define LIN_ADVANCE
    #define ADVANCE_K 0.15        // (mm) Compression length applying to all extruders
#define ADVANCED_OK
    #define X_CURRENT       1000        // (mA) RMS current. Multiply by 1.414 for peak current.
    #define X_CURRENT_HOME  X_CURRENT  // (mA) RMS current for homing. (Typically lower than *_CURRENT.)
    #define X_MICROSTEPS     16        // 0..256
    #define Y_CURRENT       1000
    #define Y_CURRENT_HOME  Y_CURRENT
    #define Y_MICROSTEPS     16
    #define Z_CURRENT       1000
    #define Z_CURRENT_HOME  Z_CURRENT
    #define Z_MICROSTEPS      8
    #define E0_CURRENT      1000
    #define E0_MICROSTEPS    16
  #define HYBRID_THRESHOLD
  #define X_HYBRID_THRESHOLD     100  // [mm/s]
  #define X2_HYBRID_THRESHOLD    100
  #define Y_HYBRID_THRESHOLD     100
  #define Y2_HYBRID_THRESHOLD    100
  #define Z_HYBRID_THRESHOLD       3
  #define Z2_HYBRID_THRESHOLD      3
  #define Z3_HYBRID_THRESHOLD      3
  #define Z4_HYBRID_THRESHOLD      3
  #define I_HYBRID_THRESHOLD       3  // [linear=mm/s, rotational=°/s]
  #define J_HYBRID_THRESHOLD       3  // [linear=mm/s, rotational=°/s]
  #define K_HYBRID_THRESHOLD       3  // [linear=mm/s, rotational=°/s]
  #define U_HYBRID_THRESHOLD       3  // [mm/s]
  #define V_HYBRID_THRESHOLD       3
  #define W_HYBRID_THRESHOLD       3
  #define E0_HYBRID_THRESHOLD     30
  #define E1_HYBRID_THRESHOLD     30
  #define E2_HYBRID_THRESHOLD     30
  #define E3_HYBRID_THRESHOLD     30
  #define E4_HYBRID_THRESHOLD     30
  #define E5_HYBRID_THRESHOLD     30
  #define E6_HYBRID_THRESHOLD     30
  #define E7_HYBRID_THRESHOLD     30
   #define TMC_HOME_PHASE { 640, 640, 640 }

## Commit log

2024-04-11 Wiring diagram and any other product information
    [17HE15-1504S.STEP]
2024-05-21 Added a full Wiring Diagram
    Items may differ from the diagram picture, the wirign should be the same nonetheless
2024-05-23 Added the final Marlin Software Config
    [Configuration.h, Configuration_adv.h, esp32.csv]
2024-05-24 Final Changes have been made
    [BOM.xlsx, BTTCase.stl, BTTTop.stl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]
2024-05-24 Added a new CAD File version
2024-05-24 New documents folder
    [BOM.xlsx]

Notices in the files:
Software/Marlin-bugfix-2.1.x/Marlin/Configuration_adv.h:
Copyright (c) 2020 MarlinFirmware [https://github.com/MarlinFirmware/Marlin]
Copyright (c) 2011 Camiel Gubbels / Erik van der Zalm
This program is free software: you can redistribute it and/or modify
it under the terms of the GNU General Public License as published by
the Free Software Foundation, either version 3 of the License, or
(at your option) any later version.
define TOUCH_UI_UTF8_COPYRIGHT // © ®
